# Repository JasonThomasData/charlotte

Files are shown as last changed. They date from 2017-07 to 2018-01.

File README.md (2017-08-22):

This is the initial code to make a robot with a Raspberry Pi. The robot will have four legs attached
to a central body, like half of a spider. The robot's legs will move in coordination so that
opposing digits move at once.

### Install

To install dependencies and build the project, run `./install.sh`
That will also clean up the build objects.

### Build

Type ```make``` and hope for the best. If it's a success, your executable will appear at
```bin/charlotte```.

When you're done, clean it up with ```make clean```.

### Tests

At the moment, all tests are for the servos. All in /bin/test_*.

### Licence

MIT Licence, all clauses apply, credit Jason Thomas 2017.

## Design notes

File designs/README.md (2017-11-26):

Download and install OpenScad to compile the `.scad` files into `.stl`.

The original files that were printed are in gen_1. The next files to test are in gen_2. When a
shape is printed, following designs are a new generation.

The gen_1 objects were printed on a MakerBot and the results were pretty good.
The settings were:

    Quality          standard
    Infill           70%
    number of shells 2
    Layer width      0.2 mm

The gen_2 objects were the same, but the infill was changed to 30%. This meant they were slightly
slighter and weaker, but cheaper also.

To test the print, check that the ScaleTest.stl prints to 8mm wide, 3mm high, circle diameter of
6mm.

Where there are non-symmetrical elements in an .stl, you'll need to print an equal number of
mirrored objects.

The WriteScad code was from [here](https://www.thingiverse.com/thing:16193)

### Printing the base

When you print the base, it will be best to use a heated glass plate. Since the shape covers such
a large area, the bottom will cool as the top is still hot and it will warp.

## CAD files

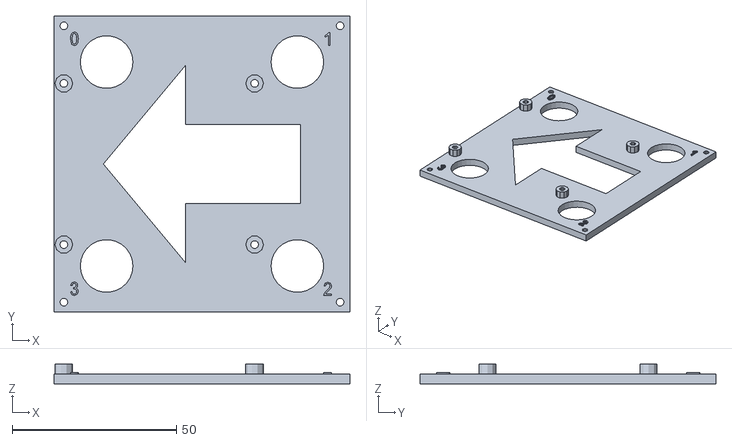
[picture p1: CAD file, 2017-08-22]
designs/base/gen_2/base#2.stl
90.0 x 90.0 x 6.00

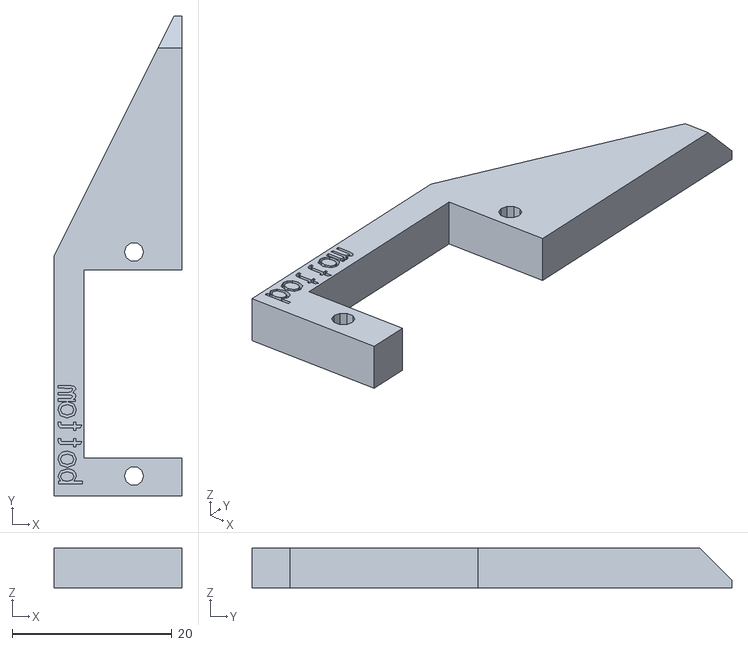
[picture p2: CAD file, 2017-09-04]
designs/leg_bottom/gen_2/leg_bottom#2_mirror.stl
16.0 x 60.0 x 5.00

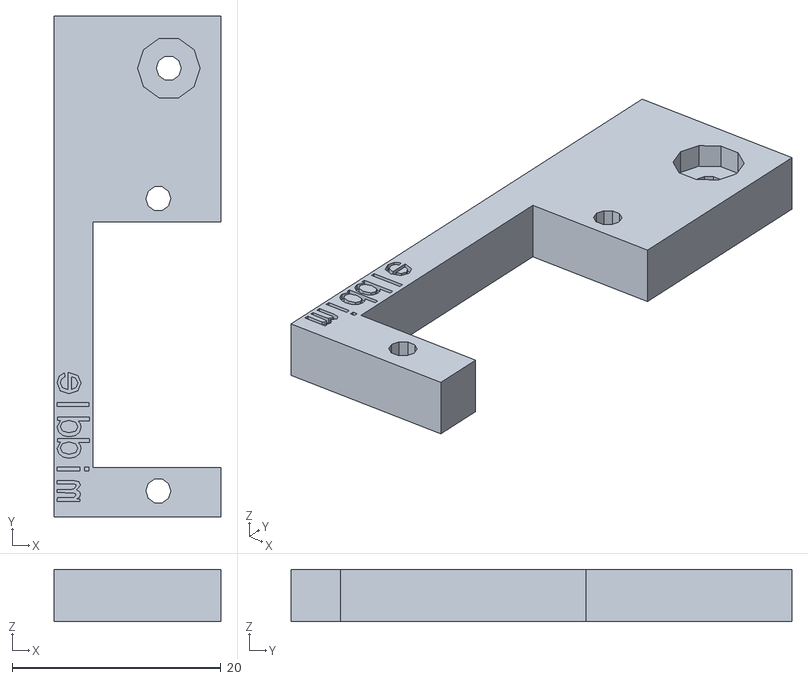
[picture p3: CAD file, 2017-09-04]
designs/leg_middle/gen_2/leg_middle#2_mirror.stl
16.0 x 48.0 x 5.00

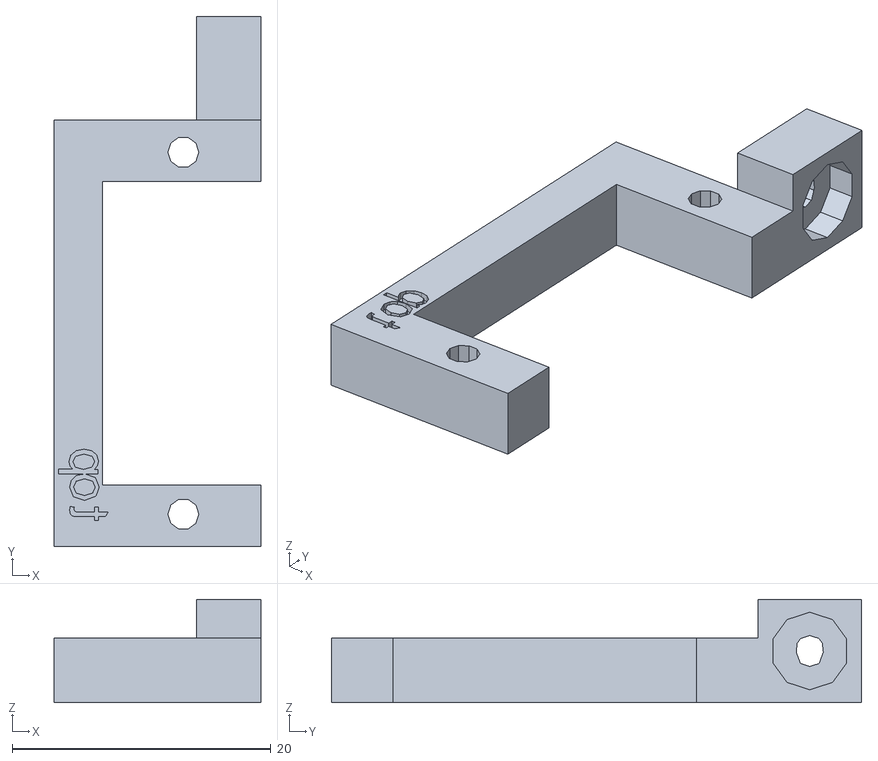
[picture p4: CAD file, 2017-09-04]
designs/leg_top/gen_2/leg_top#2_mirror.stl
16.0 x 41.0 x 8.00

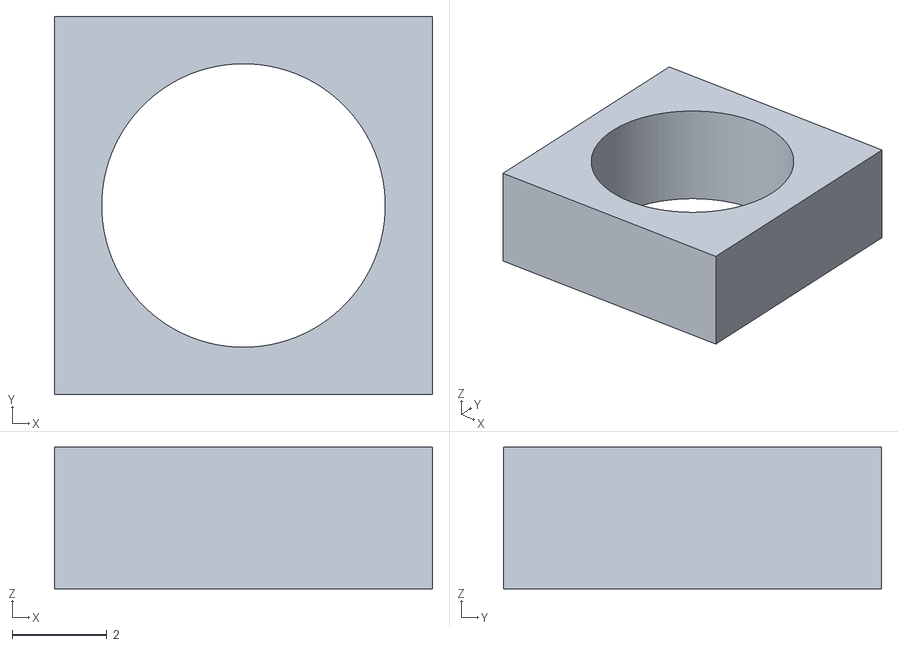
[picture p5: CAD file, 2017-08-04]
designs/ScaleTest.stl
8.00 x 8.00 x 3.00

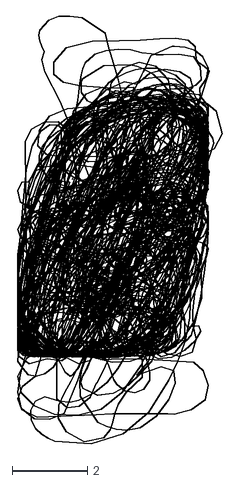
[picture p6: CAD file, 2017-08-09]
designs/Writescad/knewave.dxf
5.46 x 11.4

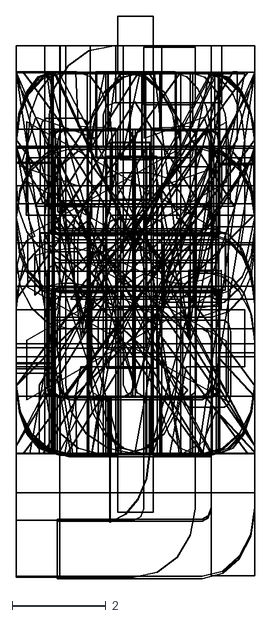
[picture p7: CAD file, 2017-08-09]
designs/Writescad/orbitron.dxf
5.08 x 12.0

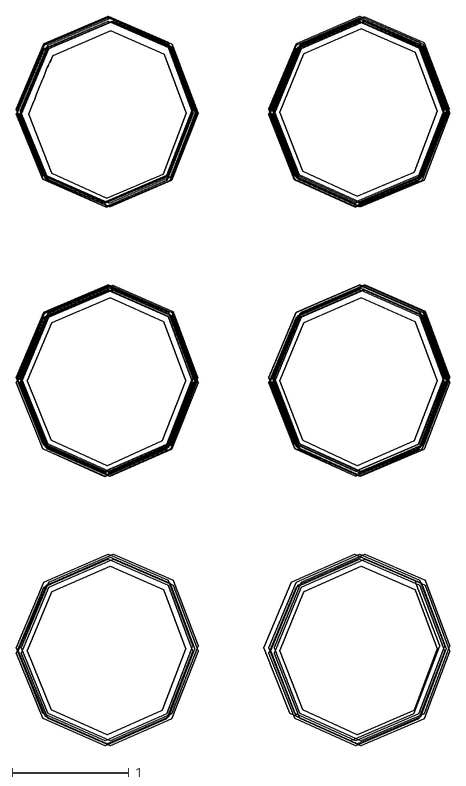
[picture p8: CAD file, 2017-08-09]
designs/Writescad/braille.dxf
3.72 x 6.26

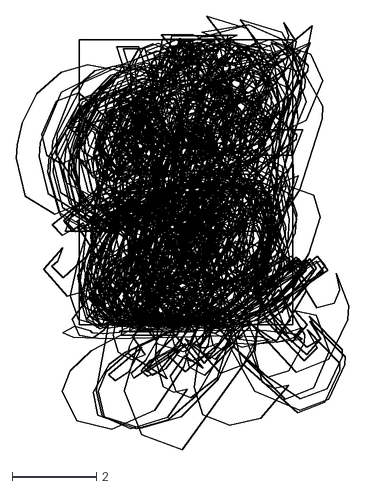
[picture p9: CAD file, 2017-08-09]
designs/Writescad/BlackRose.dxf
7.90 x 10.3

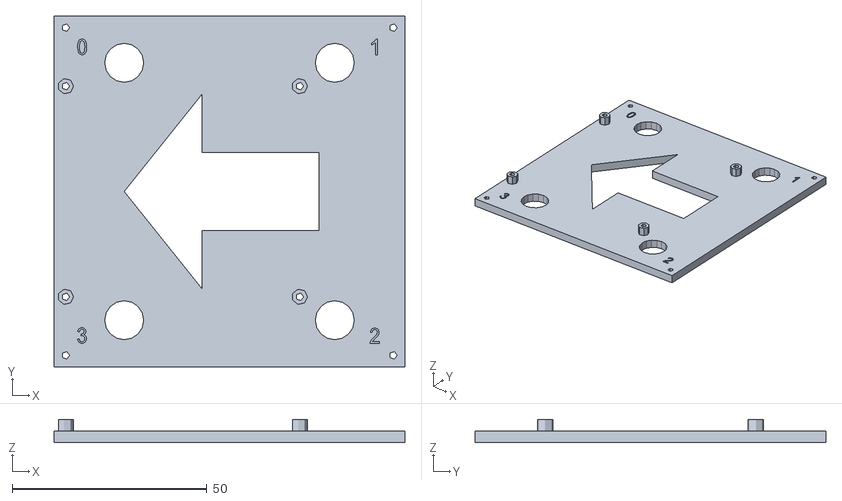
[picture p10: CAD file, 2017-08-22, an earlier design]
designs/base/gen_1/base#1.stl
90.0 x 90.0 x 6.00

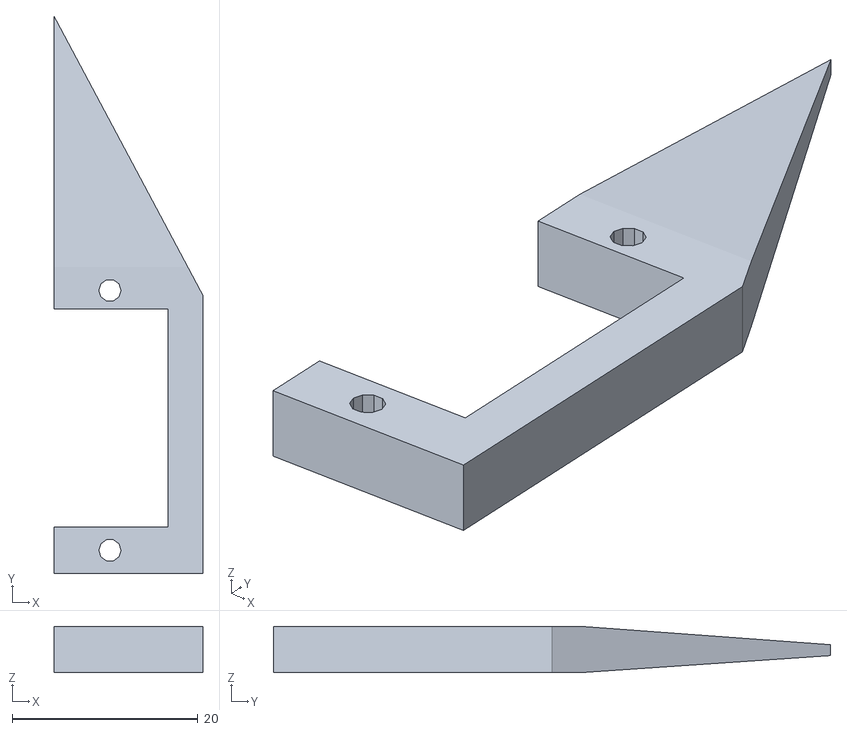
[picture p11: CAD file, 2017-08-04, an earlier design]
designs/leg_bottom/gen_1/leg_bottom.stl
16.0 x 60.0 x 5.00

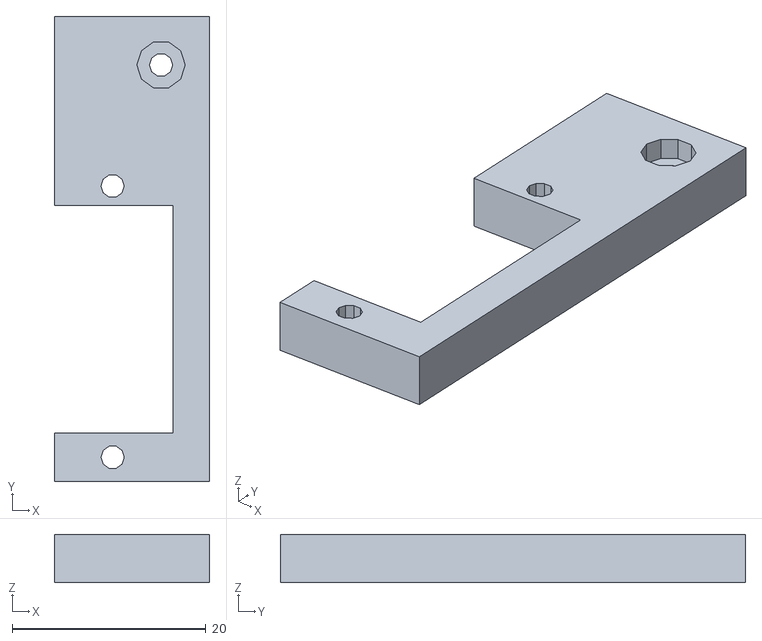
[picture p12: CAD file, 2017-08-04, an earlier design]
designs/leg_middle/gen_1/leg_middle.stl
16.0 x 48.0 x 5.00

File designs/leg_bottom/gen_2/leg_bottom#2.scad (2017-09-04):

use <../../Writescad/Write.scad>

//////////////////////////
// MOTOR - HOLDER

module screws()
{
    radius = 1.2;
    distance = 28;

    translate([0, 0])
        circle(r = radius, $fn = 10);
    translate([0, distance])
        circle(r = radius, $fn = 10);
}

module body()
{
    width = 12.5;
    length = 23.5;

    translate([-width / 2, 2.25])
        square([width, length]);
}

module motor() {
    screws();
    body();
}

//////////////////////////
// LEG

module leg(width)
{
    thickness = 5;
    length = 60;
    points = [
        [0, 0],
        [0, length],
        [1, length],
        [width, length / 2],
        [width, 0]
    ];

    linear_extrude(height = thickness)
        difference()
        {
            polygon(points = points);
            translate([6, 2.5])
                motor();
        }
}

module schampfer()
{
    y = 56;
    x = 0;
    z = 5;
    angle = -45;

    translate([x, y, z])
        rotate([angle, 0, 0])
            linear_extrude(height = 5)
                square([10, 10]);
}

module text(width, fontsize)
{
    x = width-0.5;
    y = 1.5;
    z = 4.5;

    translate([x, y, z])
        rotate([0, 0, 90])
            write("bottom", h = fontsize);
}

//////////////////////////
// GLOBALS

width = 16;
fontsize = 3;

//////////////////////////
// RENDER

difference()
{
    difference()
    {
        leg(width);
        schampfer();
    }
    text(width, fontsize);
}

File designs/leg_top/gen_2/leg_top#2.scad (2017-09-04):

use <../../Writescad/Write.scad>

//////////////////////////
// MOTOR - HOLDER

module screws()
{
    radius = 1.2;
    distance = 28;

    translate([0, 0])
        circle(r = radius, $fn = 10);
    translate([0, distance])
        circle(r = radius, $fn = 10);
}

module body()
{
    width = 12.5;
    length = 23.5;

    translate([-width / 2, 2.25])
        square([width, length]);
}

module motor()
{
    screws();
    body();
}

//////////////////////////
// LEG

module leg(width)
{
    thickness = 5;
    length = 33;
    
    points = [
        [0, 0],
        [0, length],
        [width, length],
        [width, 0]
    ];

    linear_extrude(height = thickness)
        difference()
        {
            polygon(points=points);
            translate([6, 2.5])
                motor();
        }
}

module text(width, fontsize)
{
    x = 1.2;
    y = 1.5;
    z = 4.5;

    translate([width - x, y, z])
        rotate([0, 0, 90])
            write("top", h = fontsize);
}

//////////////////////////
// SPIN SHAFT

module spin_shaft()
{
    small_radius = 1.2;
    large_radius = 3;
    small_depth = 3;
    large_depth = 2;
    x = 0;
    y = 37;
    z = 4;

    translate([x + large_depth, y, z])
        rotate([0, 90, 0])
            linear_extrude(height = small_depth)
                    circle(r = small_radius, $fn = 10);
    translate([x, y, z])
        rotate([0, 90, 0])
            linear_extrude(height = large_depth)
                circle(r = large_radius, $fn = 10);
}

module spin_shaft_socket()
{
    width = 8;
    depth = 5;
    x = 0;
    z = 8;
    y = 33;

    translate([x, y, z])
        rotate([0, 90, 0])
            linear_extrude(height = depth)
                square([width, width]);
}


//////////////////////////
// GLOBALS

width = 16;
fontsize = 3;

//////////////////////////
// RENDER

difference()
{
    spin_shaft_socket();
    spin_shaft();
}
difference()
{
    leg(width);
    text(width, fontsize);
}

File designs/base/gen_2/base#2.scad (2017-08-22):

use <../../Writescad/Write.scad>

////////////////////////
// HOLES

/* This board is to be used for a Raspberry Pi 3. The base#1
 * produced a warped board, and future prints should use a
 * heated glass plate.
 */

module screw_hole(x, y, hole_r)
{
    translate([x, y, 0])
        circle(hole_r, $fn = 10);
}

module screw_buffer(x, y, z, hole_r)
{
    outer_r = hole_r + 1.5;
    height = 3;
    translate([x, y, z])
        linear_extrude(0, 0, height)
            difference()
            {
                circle(outer_r, $fn = 10);
                circle(hole_r, $fn = 10);
            }
}

/* This is kind of the dumb way to make the holes. The Raspberry 
 * Pi holes are 49 apart along y, 58 apart along x.
 */
module all_screw_holes(hole_r)
{
    //Pi Board holes
    screw_hole(3, 20.5, hole_r);
    screw_hole(61, 20.5, hole_r);
    screw_hole(61, 69.5, hole_r);
    screw_hole(3, 69.5, hole_r);
    //leg holes
    screw_hole(3, 3, hole_r);
    screw_hole(3, 87, hole_r);
    screw_hole(87, 87, hole_r);
    screw_hole(87, 3, hole_r);
}
// Note - lots of duplication between these two, try and clean this up module
module all_screw_buffers(z, hole_r)
{
    //Pi Board buffers
    screw_buffer(3, 20.5, z, hole_r);
    screw_buffer(61, 20.5, z, hole_r);
    screw_buffer(61, 69.5, z, hole_r);
    screw_buffer(3, 69.5, z, hole_r);
}

module wire_holes(base_width)
{
    translate([16, base_width - 14, 0])
        circle(r = 8);
    translate([base_width - 16, base_width - 14, 0])
        circle(r = 8);
    translate([base_width - 16, 14, 0])
        circle(r = 8);
    translate([16, 14, 0])
        circle(r = 8);
}

////////////////////////
// BASE

module arrow()
{
    arrow_shape = [
        [0, 0],
        [25, 30],
        [25, 12],
        [60, 12],
        [60, 0]
    ];
    mirror([0, 90])
        polygon(points = arrow_shape);
    polygon(points = arrow_shape);
}

module base(base_width, base_thickness, arrow_pos)
{
    difference()
    {
        difference()
        {
            square(base_width);
            translate(arrow_pos)
                arrow(arrow_pos);
        }
        wire_holes(base_width);
    }
}

module text(base_width, base_thickness)
{
    z = base_thickness - 0.5;
    translate([5, base_width-9, z])
        write("0");
    translate([base_width-8, base_width-9, z])
        write("1");
    translate([base_width-8, 5, z])
        write("2");
    translate([5, 5, z])
        write("3");
}

////////////////////////
// GLOBALS

base_thickness = 3;
base_width = 90;
arrow_pos = [15, 45];
hole_r = 1.2;

////////////////////////
// RENDERS

linear_extrude(0, 0, base_thickness)
    difference()
    {
        difference()
        {
            base(base_width, base_thickness, arrow_pos);
        }
        all_screw_holes(hole_r);
    }
all_screw_buffers(base_thickness, hole_r);
text(base_width, base_thickness);

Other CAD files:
designs/Writescad/Letters.dxf
designs/leg_bottom/gen_2/leg_bottom#2.stl
designs/leg_middle/gen_2/leg_middle#2.stl
designs/leg_top/gen_2/leg_top#2.stl
designs/leg_top/gen_1/leg_top.stl
designs/leg_middle/gen_2/leg_middle#2.scad
designs/ScaleTest.scad
designs/Writescad/TestFont.scad
designs/Writescad/TestSurfaceText.scad
designs/Writescad/TestWrite.scad
designs/Writescad/TestWriteCube.scad
designs/Writescad/TestWriteCylinder.scad
designs/Writescad/TestWriteSphere.scad
designs/Writescad/Write-1.scad
designs/Writescad/Write.scad
designs/base/gen_1/base#1.scad
designs/leg_bottom/gen_1/leg_bottom.scad
designs/leg_middle/gen_1/leg_middle.scad
designs/leg_top/gen_1/leg_top.scad

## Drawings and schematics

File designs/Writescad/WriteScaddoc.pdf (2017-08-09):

p1

## WriteScad

By Harlan Martin
harlan@sutlog.com
January 2012

Version 2
Added support for future font selection (default is Letters.dxf) Added WriteCube module
Added Rotate for text (rotates on the plane of the text)
Added writesphere module

NOTE: These routines require openscad version 2011.12 or later

http://www.openscad.org/

-o-

## write()

Note about strings:
1... | The quote " symbol cannot be inserted into a string alone Either use \" or just the single quote' will show as "
2... | The \ is used for special text characters, so use the bar | to show the back slash \

Usage

Put the files (write.scad) and (letters.dfx) in the
| same directory as your project.

write("Hello World!",t=3,h=5,center=true);

(t=mm) (optional) The thickness of the letters in mm.
| The default is 1mm if not specified

(h=mm)(optional) The height of the letters in mm.
| The default is 4mm if not specified

(rotate=degrees) Rotates the text along the plane it is written on.

(center=boolean) (optional) Centers the text at default coordinates. Examples:

use <write.scad> // Dont forget to include this line

//example1: Uses all declarations..
| translate([20,15,0]) write("Example 1",t=4,h=5.75,center=true);

//example2: Quick and easy
| write("That was easy!",h=12);

//example3: move and rotate(front) (remember to translate..then rotate)
| translate([0,0,10]) rotate(90,[1,0,0]) // rotate around the x axis write("Rotate +X 90 (front)",t=2);

//example4: move and rotate(left side)
| translate([0,0,20]) rotate(90,[1,0,0]) // rotate around the x axis rotate(90,[0,-1,0]) // rotate around the y axis write("Rotate +X 90 and -Y 90 (left side)");

//example5: move and rotate(right side)
| translate([0,0,30]) rotate(90,[1,0,0]) // rotate around the x axis rotate(90,[0,1,0]) // rotate around the y axis write("Rotate +X 90 and +Y 90 (right side)");

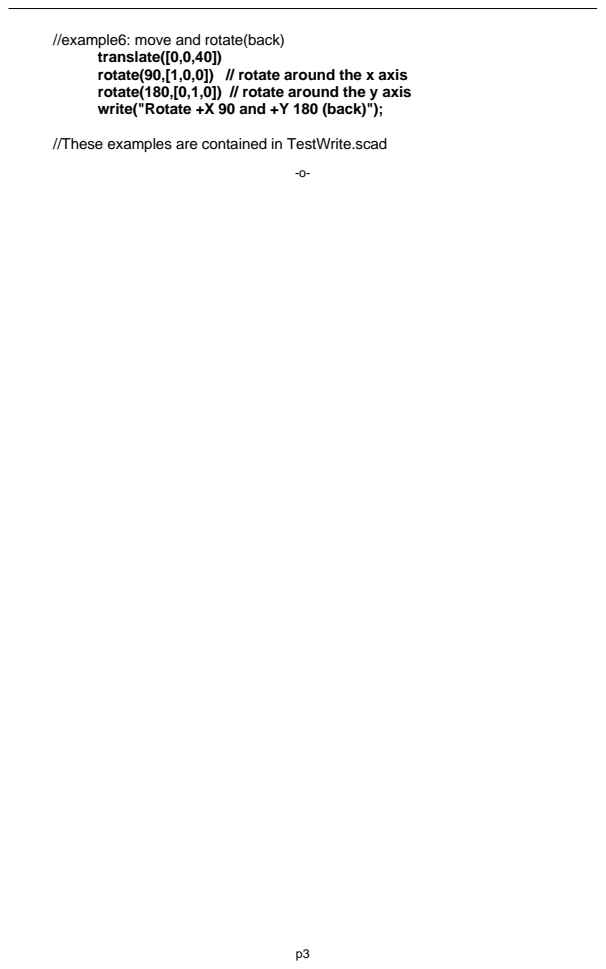
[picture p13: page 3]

//example6: move and rotate(back)

translate([0,0,40])
rotate(90,[1,0,0]) // rotate around the x axis
rotate(180,[0,1,0]) // rotate around the y axis
write("Rotate +X 90 and +Y 180 (back)");

//These examples are contained in TestWrite.scad

## writecube()

For these examples, assume we have the cube: use <write.scad>
translate([10,20,30])
cube(30,center=true);
text where and size
The values for text=, where= and size= are required, but if the values are entered in this order, then the commands are not required. These three examples produce the same results.

writecube(text="text", where=[10,20,30], size=[30,30,30]); or
writecube("text",[10,20,30], [30,30,30]);
or
writecube("text",[10,20,30],30);

text is written on the center front of a cube that is 30mm on all sides, and is centered at [10,20,30]

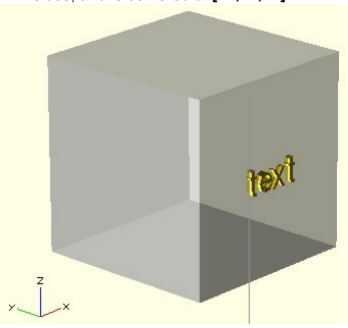
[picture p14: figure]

text="whatever text you want to write"
where= the center coordinates of the box
size = size of cube. If the cube is not square, use the format [xsize,ysize,zsize] If it is the same on all sides, just give the size ie. 30
face=
By default, writecube() will write on the front face of the box.
This assumes that x=left to right, y=front to back, z=bottom to top. To write on the other sides, use: face="top",face="bottom",face="back",face="front", face="left" or face="right"

writecube("Howdy!!",[10,20,30],30,face="left");

will print Howdy!! on the center left of the box.

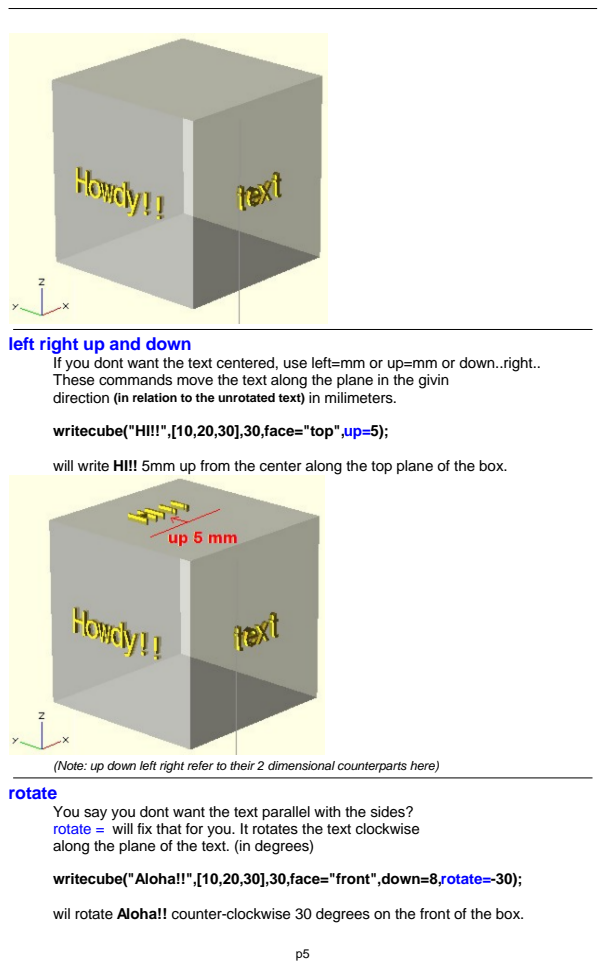
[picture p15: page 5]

left right up and down

If you dont want the text centered, use left=mm or up=mm or down..right..
These commands move the text along the plane in the givin
direction (in relation to the unrotated text) in milimeters.

writecube("HI!!",[10,20,30],30,face="top",up=5);

will write HI!! 5mm up from the center along the top plane of the box.

(Note: up down left right refer to their 2 dimensional counterparts here)
rotate

You say you dont want the text parallel with the sides?
rotate = will fix that for you. It rotates the text clockwise
along the plane of the text. (in degrees)

writecube("Aloha!!",[10,20,30],30,face="front",down=8,rotate=-30);

wil rotate Aloha!! counter-clockwise 30 degrees on the front of the box.

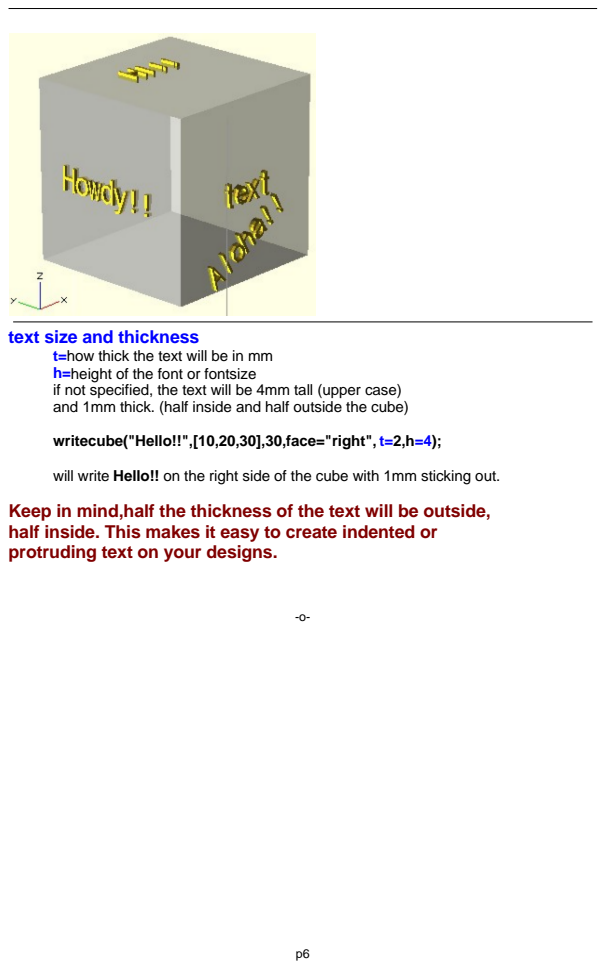
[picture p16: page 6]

text size and thickness

t=how thick the text will be in mm
h=height of the font or fontsize
if not specified, the text will be 4mm tall (upper case)
and 1mm thick. (half inside and half outside the cube)

writecube("Hello!!",[10,20,30],30,face="right", t=2,h=4);

will write Hello!! on the right side of the cube with 1mm sticking out.
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

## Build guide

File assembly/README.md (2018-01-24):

These are the instructions for piecing together the hardware components of the robot.

### Materials

- 12 x sg90, Tower Pro, 180-degrees servo motors
- 36 female-male prototype wires. Prefer 12 black, 12 red and 12 different colours
- 1 x Raspberry Pi 3
- 1 x SD card, I think >= 8GB is good
- 1 x Arch Linux ARM 64b image, headless
- 2 x each leg component of the latest generation, 3D printed, check in designs (there should be 12 in total)
- 1 x base component, 3D printed
- 24 x M2 nuts and bolts, no less than 10mm in length

Installing Arch linux on the SD card is a job in itself, and there's a separate explainer [here]().

For the 3d-printed components, be sure to read the specs for each... the components will be light and strong enough.

### Assembling a servo and component (holder)

The servo shafts should be at the top end of the leg. See this arrangement of a middle component.

![pic_of_servo_assembly]()

### Assembling a leg

Each leg has three main parts, each consisting of a servo and a brace to hold it. Group them by whether or not they're file names include 'mirror' or not.

Each leg should have three servos, and each servo has its own signal wire, to receive PWM signals from the board. It should be orange, and there should also be a positive red and black ground wire. 

Have a look at this configuration, this is one of the normal legs without 'mirrored' in the filename.

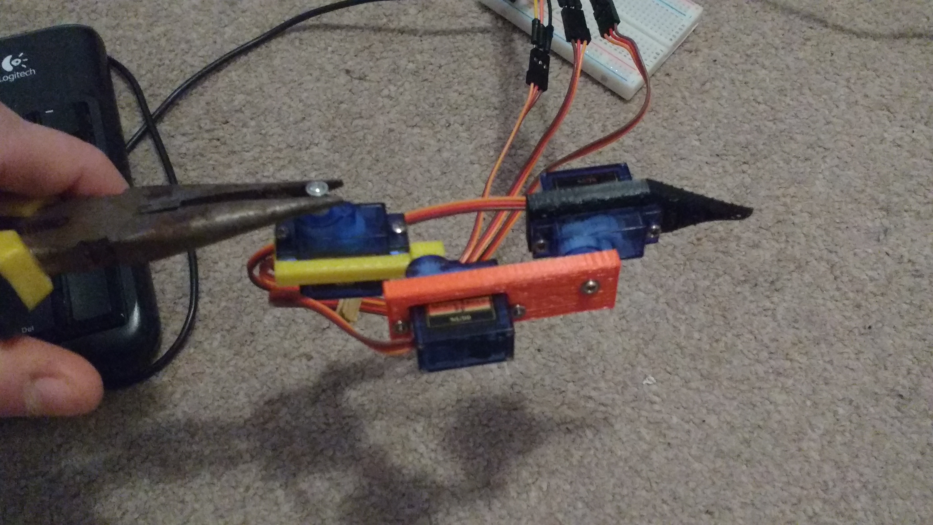
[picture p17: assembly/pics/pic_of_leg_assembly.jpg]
pic_of_leg_assembly


The servos will each come with one or more screws when you purchase them, and you can file down the tips of those screws to be more flat, so each is more like a bolt.

Screw them into the servo shafts, but not tight at first. It's important they're not tight at first, because you want to make sure the servo shafts are at the right angle before that.

You will want to know what the board's pin configuration is at this point, and the simplest way is to enter `GPIO` at the terminal. It should give you a table of your board's pin config. Use the wiringPi pin numbers.

For a normal leg, which is not a mirrored leg, use the Pi board's pins 0 (bottom), 1 (middle), and 2 (top) for the signal wires. When the servos are all connected run `./bin/test_leg`.

For a mirrored leg, it's the same, but you want to use pins 3 (bottom), 4 (midddle) and 5 (top), and run bin/leg_1_test -- this is no longer the case, update this

Each servo in each leg will do a series of things and then stop at the positions where the leg would be fully extended, so, you can now put the leg on a flat surface and screw the screws in tighter. You might want to use a mild adhesive, like some kind of thread-tight solution to make the screw, shaft and leg component stay in place.

With all servos screwed in tight, you can now hold the remaining servo shaft with a sideways pair of plyers, and the leg will do a complete turn walk cycle and then return to the fully extended position.

### Assembling the robot

With all the legs in place, you can screw the top servos underneath the printed board. The circle on the robot's base is for the servo's wires to feed through, and the wires should come out the top.

pic_of_attached_leg

The board, near each corner screw hole, has numbers. The normal, non-mirror legs, should be at positions 0 and 2, and the mirrored legs should go at positions 1 and 3. Leg 0 will be the front-right leg on the forward-facing robot, and the arrow is good if you're unsure. The legs go clockwise 0-3

Here's the board's pin arrangement for each leg:

    0:
        bottom: 0
        middle: 1
        top: 2
    1:
        bottom: 3
        middle: 4
        top: 5
    2:
        bottom: 6
        middle: 7
        top: 8
    3:
        bottom: 9
        middle: 10
        top: 11

You can change those pin numbers, and the place to do that is in the RobotFactory, but I don't see a need.

The first, leg 0, will be the front-right leg on the forward-facing robot, (the arrow is no accident) and the legs will continue around in a clockwise fashion.

I used a small breadboard in my robot, but you can do what you want, because I'm not your dad and can't tell you how to live your life.

Your robot should not power its servos from the board's power supply. Doing so creates a serial circuit and the board will turn off. The servos should have access to a 3.3v power supply. That supply's positive wire should come into one pin on the board and go out to the 12 servo's positive wires, on the same rail so the wires are all connected in parallel. Same for negative.

The servos shouldn't do anything until they get sent a signal and they've got their own internal relay for that, but I guess you could choose to have a power supply switch.

For protecting the pins of the Pi board, it's good to have a resistor for the signal wire, and 1k ohm seems to work well. This is the reason I chose to have a breadboard so doing the resistor thing is easy.

Here's what the board

### Power

I'm still figuring this one out.

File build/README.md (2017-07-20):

This is where the build objects go. Can be made clean with make clean

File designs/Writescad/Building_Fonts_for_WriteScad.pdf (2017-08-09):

p1

Harlan Martin

## Intro

Let me begin this by apologizing to everyone that uses InkScape.. These instructions are geared toward people like me that have never used it before. EVERYTHING in this help file is step by step. If there is a better way of doing it, let me know and I will revise the instructions.

Be forewarned... Making fonts is very tedious, but once you build a couple of letters, it's not very difficult. I tried to cover all the problems that I encountered while I was making fonts, but I might have missed a few. If so, contact me on Thingiverse (harlandmii) . Someone else might have the same problems.

Note: If you do take the time to build a font, PLEASE share it!!!!! I and anyone else that use it would be grateful :)

If you have problems, check the help section... I will try to keep it as updated as possible.

-o-

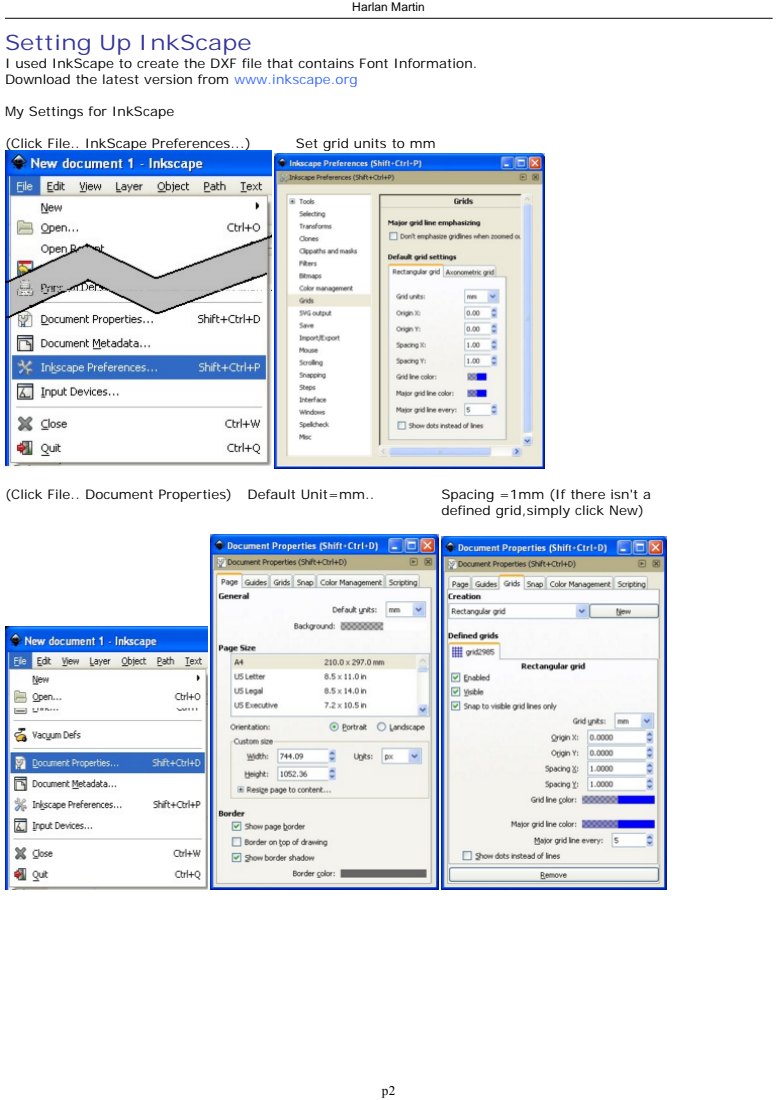
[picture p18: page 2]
(Click File.. InkScape Preferences...); Set grid units to mm; (Click File.. Document Properties); Default Unit=mm..; Spacing =1mm (If there isn't a

Setting Up InkScape
I used InkScape to create the DXF file that contains Font Information.
Download the latest version from www.inkscape.org

My Settings for InkScape

defined grid,simply click New)

To view the layers window.. (click Layer.. Layers)

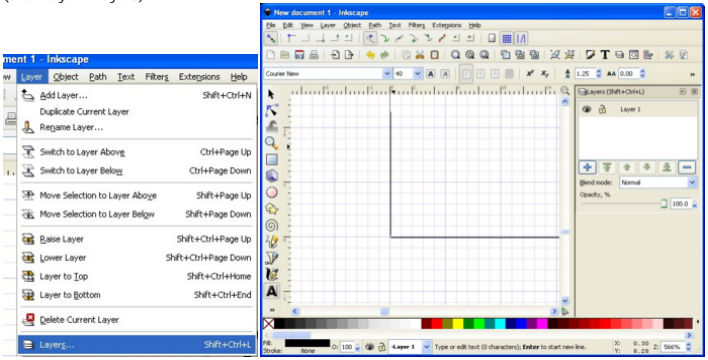
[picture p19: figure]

-o-

## Making a Guide

Click Create Text

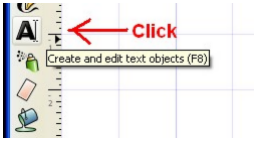
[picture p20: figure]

At the top of inkscape, Choose Desired Font and set font size to 40 (I also selected bold because courier is a thin font)

The first letter needs to be one of the larger letters, (Like capital M or W) so we can make a bounding guide to align the rest of the letters.

I am zoomed in pretty close here (1mm squares) Click in the bottom left of the page marker

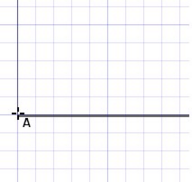
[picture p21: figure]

Type M

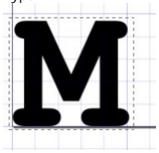
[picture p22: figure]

Use the Arrow (select and transform)
to align the letter to the left and bottom of the page marker.

Rename Layer 1 to the name of the letter

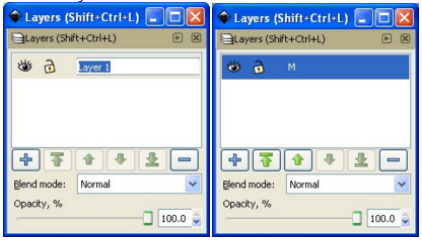
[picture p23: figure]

On the layers window, click the + to add a new layer. (Name it Border or something similar)
Use the Green Down Arrow to move it to the bottom of the list.

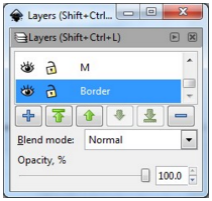
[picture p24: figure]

Make sure the Border layer is selected in the layers window. Click Create Rectangle and make a bounding box for the M
(I chose light pink)
All of the rest of the letters will be centered in this box.

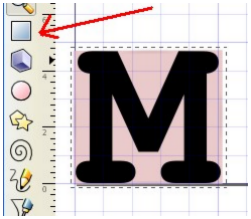
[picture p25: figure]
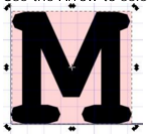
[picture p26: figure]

Use the Arrow to select the box

Click Path... Object to Path

Use Edit paths by nodes.
and select all four corners

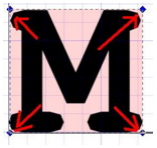
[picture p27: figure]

Click Make selected segments lines
(This process will be used on each letter to convert them to lines)

Lock the Border layer so it can't be accidentally changed.

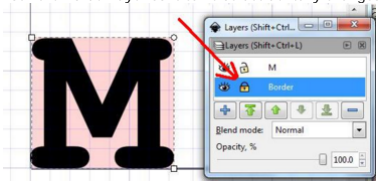
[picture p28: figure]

Choose the letter (M) Layer again..

Click the arrow (Select and transform) Click on the letter to select it

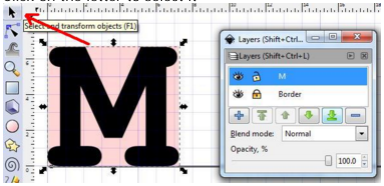
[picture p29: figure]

Click Path and Object to Path

Click Edit paths by nodes..
Then click on the letter to select it.

Drag a square around the letter to select all the nodes

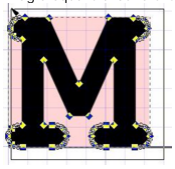
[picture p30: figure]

Click Make selected segments lines

If everything looks ok, we can go to the next letter. (If not, see the section on Making Letters Better)

-o-

## Making Letters

## Repeat the following steps for all letters and symbols

Click the + on the layers window to make a layer for
the next letter. (If its an A, name the layer A)
(lower case letter layers are named with a lower case letter and an underscore ie... the layer for lower case c would be c_ )
(layers are case sensitive)
(use the green arrows to put the layers in order if desired)

Close the eye on the M layer to hide it..
Then choose the A layer to edit

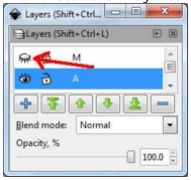
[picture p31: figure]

Choose create and edit text objects

Type the letter (A)

Use the Arrow to align it

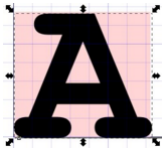
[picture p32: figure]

Click Path and Object to Path

Click edit paths by nodes
Click on the letter, then select all the nodes

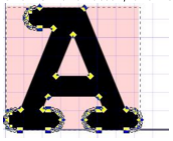
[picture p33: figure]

Click Make selected segments lines

### (That is the process for each letter)

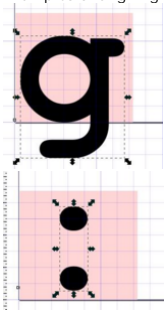
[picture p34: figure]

Examples of aligning letters

-o-

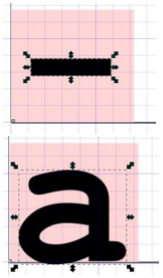
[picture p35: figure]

## Making Letters Better

Somtimes, when you click Path..Object to path, the image won't have enough points to make curved sides.

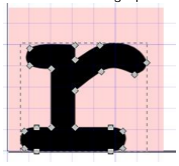
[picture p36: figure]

After you select all the nodes and click

Make Selected Segments Lines,
it becomes obvious.

If you don't like the looks of the letter, hold Ctrl and press Z to undo the change.

Click Edit paths by nodes
Select 2 or more nodes
(tip:click one node, then hold shift and click another) Then click Insert new nodes into selected segments.

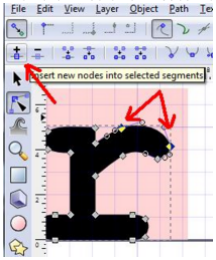
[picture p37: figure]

A new node will be on the curve.

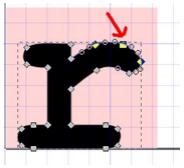
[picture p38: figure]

Repeat this process on each area that doesnt have enough
nodes to make the curves look smooth.

### NOTE: The more nodes a letter has, the slower it will draw in

OpenScad. The fewer, the better.

When your done adding nodes, select them all, and

click Make selected segments lines

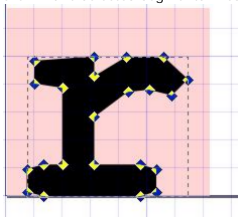
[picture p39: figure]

Move on to the next letter

-o-

## Saving the File

Be sure to save the SVG file each time.. Just click file.. Click save Name the file with the name of the font.

To use the font in OpenScad, we need to convert it to a DXF file.
Before saving the DXF, verify that all letters,boxes and shapes are converted to line segments. Otherwise, OpenScad won't be able to use it.

To make the DXF file:
Click File...
Click Save As...
Click the down arrow on save as type.. Choose Desktop Cutting Plotter(R13)(*.dxf)

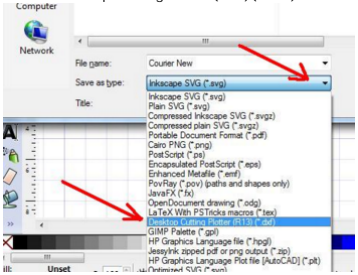
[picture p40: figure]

Click OK

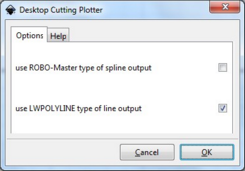
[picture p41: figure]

## Note: If you are testing a font as you create it, clear the cache on OpenScad the next time you update the Font... New letters won't appear until you do. (on OpenScad, click Design..click Flush Caches)

-o-

## HELP!!!

I will add this as soon as possible

-o-

## Testing While Making Fonts

-o-

## Font File Doesnt Work

-o-

## Some Letters Are Missing

-o-

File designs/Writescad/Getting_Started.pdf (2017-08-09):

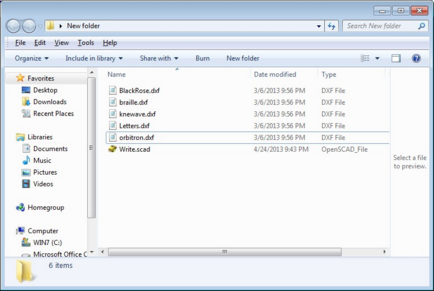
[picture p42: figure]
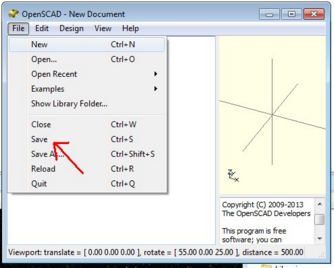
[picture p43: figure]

p1

Harlan

## Getting Started

Create a new folder on your desktop..

copy the folowing files to the new folder: Write.scad
BlackRose.dxf
braille.dxf
knewave.dxf
Letters.dxf
orbitron.dxf

Start openscad
click file.. save..

Find the new folder you created on your desktop and save your blank openscad file..

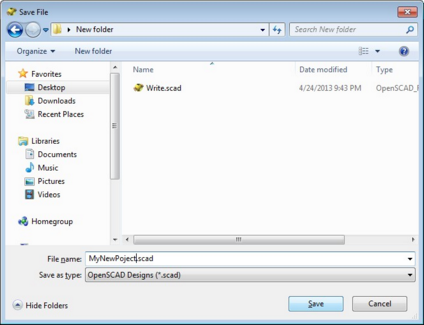
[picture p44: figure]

Your working folder (the new one you created on the desktop) will now contain write.scad, the dxf files (fonts) and your new project.

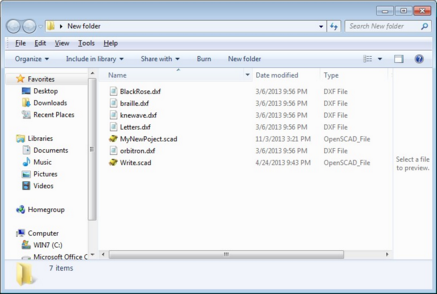
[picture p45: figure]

Now lets create an example.

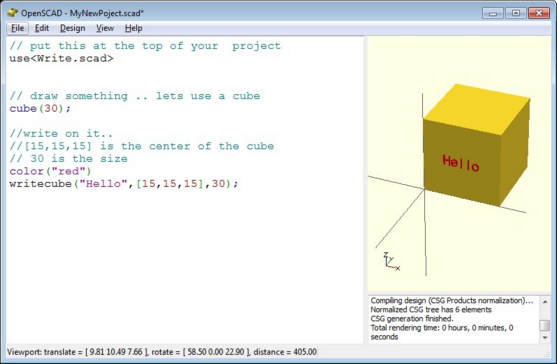
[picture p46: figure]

The use<Write.scad> tells openscad to use the routines in the write.scad file with the project you are working on..

-o-

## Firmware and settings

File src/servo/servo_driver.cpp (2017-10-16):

#include <softPwm.h>
#include <wiringPi.h>
#include <iostream>

#include "servo_driver.h"

ServoDriver::ServoDriver(int pin_number)
{
    range = 100; //Not application logic, this is a wiringPi setting. This works for the positions
    config_pin(pin_number);
}

/* The servos have a range of 180 degrees, there are ten 21 possible stages plus off */

void ServoDriver::config_pin(int pin_number_init)
{
    pin_number = pin_number_init;
    pinMode(pin_number, OUTPUT);
    digitalWrite(pin_number, LOW);
    softPwmCreate(pin_number, 0, range);
}

void ServoDriver::off()
{
    int off_signal = 0;
    softPwmWrite(pin_number, off_signal);
}

void ServoDriver::goto_0_degrees()
{
    int pwm_signal = 23;
    softPwmWrite(pin_number, pwm_signal);
}
void ServoDriver::goto_27_degrees()
{
    int pwm_signal = 20;
    softPwmWrite(pin_number, pwm_signal);
}

void ServoDriver::goto_45_degrees()
{
    int pwm_signal = 18;
    softPwmWrite(pin_number, pwm_signal);
}

void ServoDriver::goto_54_degrees()
{
    int pwm_signal = 17;
    softPwmWrite(pin_number, pwm_signal);
}

void ServoDriver::goto_63_degrees()
{
    int pwm_signal = 16;
    softPwmWrite(pin_number, pwm_signal);
}

void ServoDriver::goto_90_degrees()
{
    int pwm_signal = 13;
    softPwmWrite(pin_number, pwm_signal);
}

void ServoDriver::goto_117_degrees()
{
    int pwm_signal = 10;
    softPwmWrite(pin_number, pwm_signal);
}

void ServoDriver::goto_126_degrees()
{
    int pwm_signal = 9;
    softPwmWrite(pin_number, pwm_signal);
}

void ServoDriver::goto_135_degrees()
{
    int pwm_signal = 8;
    softPwmWrite(pin_number, pwm_signal);
}

void ServoDriver::goto_153_degrees()
{
    int pwm_signal = 6;
    softPwmWrite(pin_number, pwm_signal);
}

void ServoDriver::goto_180_degrees()
{
    int pwm_signal = 3;
    softPwmWrite(pin_number, pwm_signal);
}

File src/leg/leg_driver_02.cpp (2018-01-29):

#include <memory>

#include "leg_driver_02.h"

// NOTE - To save future confusion, this is the prototype leg.

LegDriver_02::LegDriver_02(IServoDriver* bottom_to_add,
                           IServoDriver* middle_to_add,
                           IServoDriver* top_to_add)
{
    bottom_servo = bottom_to_add;
    middle_servo = middle_to_add;
    top_servo = top_to_add;
}

void LegDriver_02::up()
{
    bottom_servo->goto_27_degrees();
    middle_servo->goto_27_degrees();
    top_servo->off();
}

void LegDriver_02::down()
{
    bottom_servo->goto_90_degrees();
    middle_servo->goto_135_degrees();
    top_servo->off();
}

void LegDriver_02::extend_flat()
{
    bottom_servo->goto_135_degrees();
    middle_servo->goto_90_degrees();
    top_servo->off();
}

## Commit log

2017-07-20 Leg will driver the servo drivers.
2017-07-20 Servo drivers will interact with servos and Rasp Pi pins
2017-08-04 Adding designs of legs for robot, split into generations for context+history etc (for now).
    [ScaleTest.scad, ScaleTest.stl, leg_bottom#2.scad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]
2017-08-09 Updating these files to have writing on them, no fonfusion.
    [leg_bottom#2.scad, leg_bottom#2.stl, leg_middle#2.scad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]
2017-08-09 new files, base will hold Pi and legs together.
    [base#1.scad, base#1.stl]
2017-08-09 This is third party stuff, but not for the robot so doesn't belong in lib/
    [BlackRose.dxf, Letters.dxf, TestFont.scad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]
2017-08-09 Adding wires holes to the base, for motor wires
    [base#1.scad, base#1.stl]
2017-08-09 Adding pic of what the leg should look like before screwing screws tight
2017-08-09 Updating radius of each shaft
    [leg_middle#2.scad, leg_middle#2.stl, leg_top.stl]
2017-08-09 Had the name wrong, top not bottom
    [leg_top.scad, leg_top.stl]
2017-08-12 Adding new designs after the gen_1 didn't print as expected.
    [base#2.scad, base#2.stl]
2017-08-12 Changes to board to make screw holes correct, small refactor.
    [base#2.scad, base#2.stl]
2017-08-12 Changing schampfer, and refactored this
    [leg_bottom#2.scad, leg_bottom#2.stl]
2017-08-12 Refactor for the middle segment.
    [leg_middle#2.scad, leg_middle#2.stl]
2017-08-12 Removing this from the #1, this was never part of the design
    [leg_top#2.scad, leg_top#2.stl, leg_top.scad]
2017-08-12 Didn't render properly, so do again.
    [base#2.stl]
2017-08-22 Created an individual test for a servo, for testing the 12 new ones.
2017-08-22 Too much detail about servo in leg. Made better servo interface to hide details.
    [servo_driver.cpp, test_servo.cpp]
2017-08-22 Optimised positions for servos - 3(0), 13(90), 23(180)
2017-09-04 It's now possible to put the writing on top
    [leg_bottom#2.scad, leg_bottom#2.stl, leg_middle#2.scad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]
2017-09-04 Needed to print two lots of opposite legs
    [leg_bottom#2_mirror.stl, leg_middle#2_mirror.stl, leg_top#2_mirror.stl]
2017-10-16 Split leg into parts so abstract class is inherited, not duplicated
2017-10-16 I had the angles and PWM values completely wrong
    [servo_driver.cpp]
2017-10-16 Adding new leg files to Makefile
2018-01-24 Removing function (YAGNI), correcting angle issues
    [leg_driver_02.cpp, leg_driver_13.cpp]
2018-01-27 Framework for doing tests
2018-01-27 For mocking the servo_driver, used for testing the leg
2018-01-27 First test for leg, mocked servo_driver
2018-01-28 References did not work for using heap memory, pointers instead
    [leg_driver_02.cpp, leg_driver_13.cpp]
2018-01-28 Trying to use a mocking framework with pointer args
2018-01-28 Trying another framework for mocking
2018-01-29 Some basic logic to get the leg moving
2018-01-29 Some tests for making sure legs move in order
2018-02-09 Adding terminal args to test every leg
